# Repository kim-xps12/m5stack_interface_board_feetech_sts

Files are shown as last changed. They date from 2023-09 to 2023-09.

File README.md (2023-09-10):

# Feetech STS interface board for M5Stack

## About
M5StackからFeetech STSシリーズのシリアルサーボを操作するためのオリジナル基板です．KiCAD 7で設計しました．FE-URT-1([秋月リンク](https://akizukidenshi.com/catalog/g/gM-16295/))のUART機能のみを取り出して実装したため，同基板と比較して小型に収まっています．

## Appearance
**組み立て前**
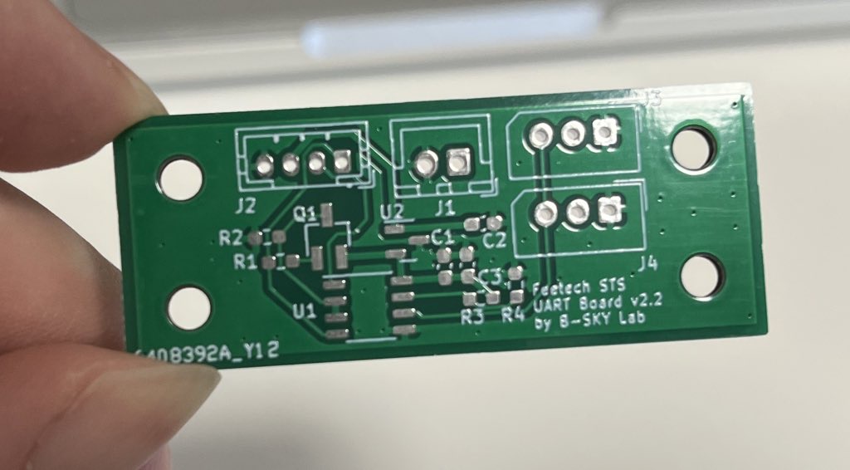
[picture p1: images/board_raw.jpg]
raw board

**完成品**
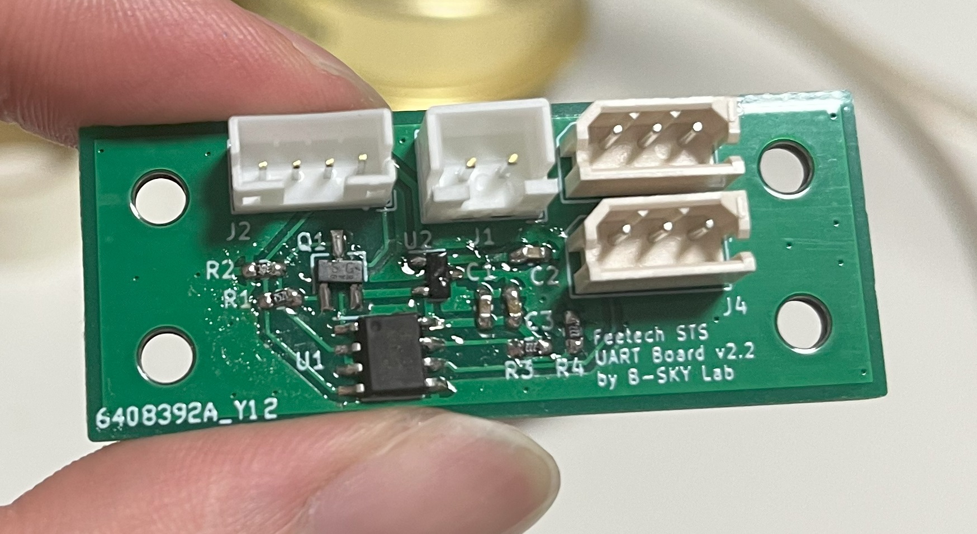
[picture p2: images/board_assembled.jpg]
assembled board

## Usage
配線と動作の様子はこちら．
https://www.youtube.com/watch?v=_5FpvqL4ExI

動作確認用にM5Stack向けのサンプルコードをm5stack_uart_feetech_stsのリポジトリ（[リンク
](https://github.com/kim-xps12/m5stack_uart_feetech_sts/)）にて公開しています．よろしければご利用ください．

## schematics

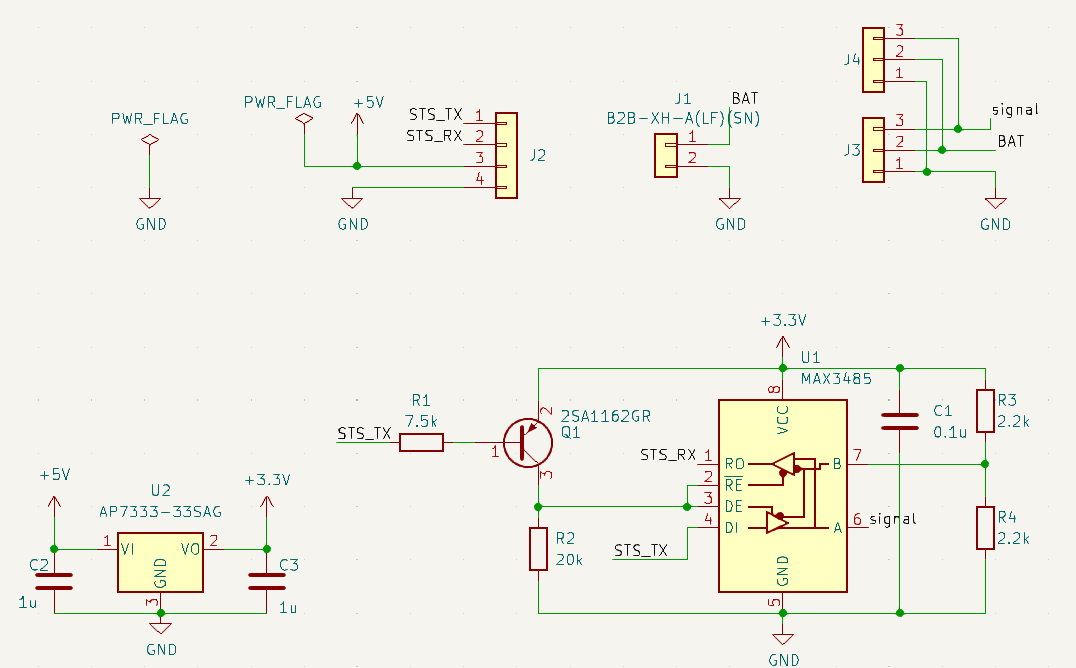
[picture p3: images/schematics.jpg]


## BOM
| Symbol | Model Number |URL, Values|
| --- | --- | --- |
| Q1  | 2SA1162GR<br> | [https://akizukidenshi.com/catalog/g/gI-02702/](https://akizukidenshi.com/catalog/g/gI-02702/)<br> |
| U1  | MAX3485ED<br> | [https://akizukidenshi.com/catalog/g/gI-16211/](https://akizukidenshi.com/catalog/g/gI-16211/)<br> |
| U2  | AP7333<br> | [https://akizukidenshi.com/catalog/g/gI-11360/](https://akizukidenshi.com/catalog/g/gI-11360/)<br> |
| J1  | JST B4B-PH-K-S(LF)(SN) | [https://www.sengoku.co.jp/mod/sgk\_cart/detail.php?code=4DK2-SDDB](https://www.sengoku.co.jp/mod/sgk_cart/detail.php?code=4DK2-SDDB)<br> |
| J2  | JST B2B-XH-A(LF)(SN) | [https://akizukidenshi.com/catalog/g/gC-12247/](https://akizukidenshi.com/catalog/g/gC-12247/)<br> |
| J3  | Molex 5267-03A-X | [https://www.sengoku.co.jp/mod/sgk\_cart/detail.php?code=EEHD-0HWA](https://www.sengoku.co.jp/mod/sgk_cart/detail.php?code=EEHD-0HWA)<br> |
| R | 0608 inch / 1608 jis metric | R1=7.5k, R2=20k, R3=R4=2.2k |
| C | 0608 inch / 1608 jis metric | C1=0.1 u, C2=C3=1u |

## Distribution
本基板（部品未実装）はboothで頒布中です．よろしければご利用ください．
https://b-sky-lab.booth.pm/items/5083992

## Reference
Feetechインターフェースボード回路図
https://akizukidenshi.com/download/ds/akizuki/feetech_digital_servo_20220729.pdf

## Disclaimer
MITライセンスでの公開です．本設計および頒布した基板において生じた一切の損害等について作者は責任を負いません．予めご了承ください．

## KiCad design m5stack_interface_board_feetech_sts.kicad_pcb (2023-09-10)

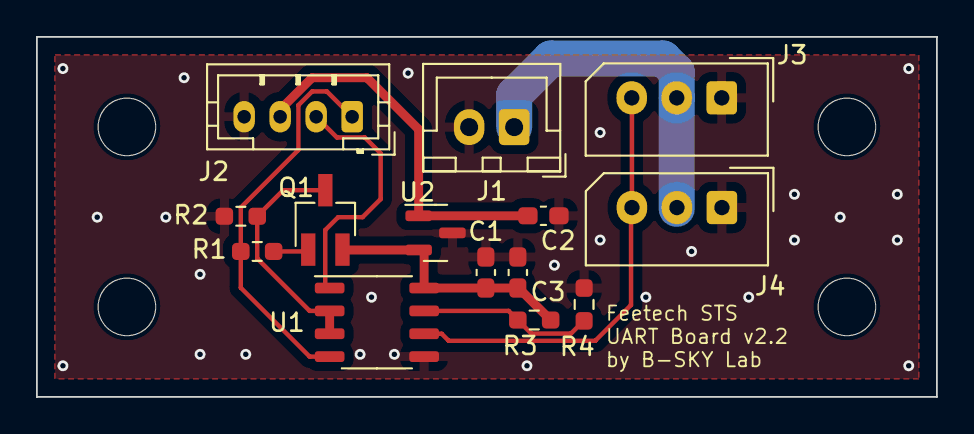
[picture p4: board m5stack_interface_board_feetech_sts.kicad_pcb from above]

Board: 2 copper layers, 50.0 x 20.0 mm, 18 parts (0 on the bottom side), 10 nets.

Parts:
C1: 0.1u; C_0603_1608Metric_Pad1.08x0.95mm_HandSolder
C2, C3: 1u; C_0603_1608Metric_Pad1.08x0.95mm_HandSolder
J1: B2B-XH-A(LF)(SN); JST_XH_B2B-XH-A_1x02_P2.50mm_Vertical
J2: B4B-PH-K-S(LF)(SN); JST_PH_B4B-PH-K_1x04_P2.00mm_Vertical
J3, J4: 22035035; Molex_SPOX_5267-03A_1x03_P2.50mm_Vertical
MH1, MH2, MH3, MH4: MountingHole_3.2mm_M3
Q1: 2SA1162GR; SC-59_Handsoldering
R1: 7.5k; R_0603_1608Metric_Pad0.98x0.95mm_HandSolder
R2: 20k; R_0603_1608Metric_Pad0.98x0.95mm_HandSolder
R3, R4: 2.2k; R_0603_1608Metric_Pad0.98x0.95mm_HandSolder
U1: MAX3485; SOP-8_3.9x4.9mm_P1.27mm
U2: AP7333-33SAG; SOT-23

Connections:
+3.3V: C1.1, C3.1, Q1.2 (E), R3.2, U1.8 (VCC), U2.2 (VO)
+5V: C2.1, J2.3, U2.1 (VI)
/BAT: J1.1, J3.2, J4.2
/STS_RX: J2.2, U1.1 (RO)
/STS_TX: J2.1, R1.1, U1.4 (DI)
/signal: J3.3, J4.3, U1.6 (A)
GND: C1.2, C2.2, C3.2, J1.2, J2.4, J3.1, J4.1, R2.1, R4.1, U1.5 (GND), U2.3 (GND)
unnamed: Q1.1 (B), R1.2
unnamed: Q1.3 (C), R2.2, U1.2 (~RE), U1.3 (DE)
unnamed: R3.1, R4.2, U1.7 (B)

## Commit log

2023-08-10 1st commit, complete to desing v1.0
    [bom.csv, designators.csv, grove_feetech_sts.dsn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]
2023-09-10 complete to design ver. double molex (#1)
    [bom.csv, designators.csv, grove_feetech_sts.kicad_pcb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]
2023-09-10 update README about KiCAD
